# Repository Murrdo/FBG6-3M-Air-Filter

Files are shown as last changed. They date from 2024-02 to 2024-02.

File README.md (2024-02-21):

# FBG6-3M-Air-Filter
Air filter for FBG6

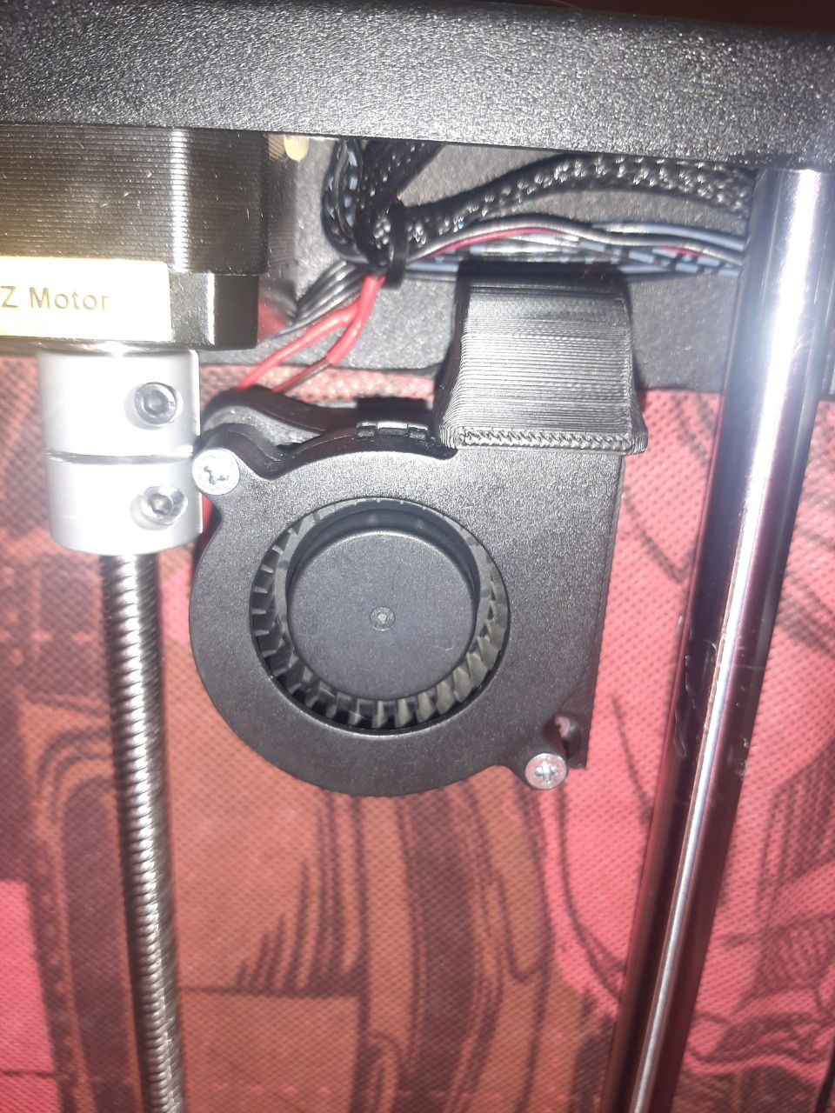
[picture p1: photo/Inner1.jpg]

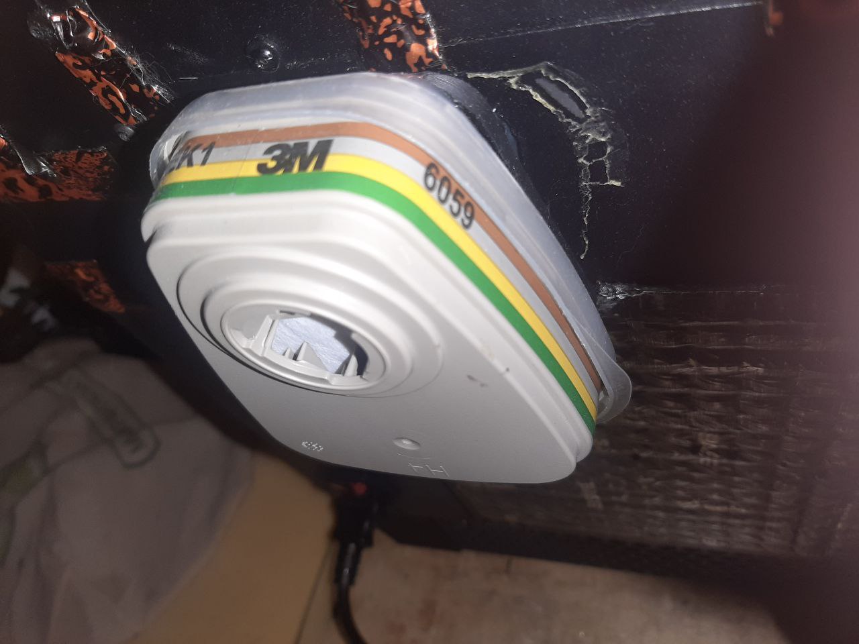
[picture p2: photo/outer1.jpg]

Фильтр для принтера FBG6 испоьзующий сменные фильтры 3M (проверено на 6059) - при условии общей герметизации запаха нет при 10 часовой печати в закрытой непроветриваемой комнате.

Подготовка и принцип действия.
<br>Фильтр работает при принципу "подпора" внешним давлением, т.е. во время работы вентилятор создаёт минимальное разряжение внутри, что бы через щели (которые в любом случае остануться) воздух снаружи поступал внутрь, а не выходил наружу. При этом ущерба темпиратуре в камере он не наносит.

Фильтр обазтельно требует акриловый колпак.

Что необходимо проклеить виброй или любым другим удобным материалом:
<br>1.Кромку примыкания двери и корпуса (очень мягкая вспененая резина толщиной 3мм)
<br>2.Колпак по периметру примыкания к корпусу (та же резина)
<br>3.Отсек с электроникой
<br>4.Щели на дне камеры
<br>5.Все отверстия под хомуты, под провод на датчик филамента и т.д. в общем вообще все мельчашие отверстия/щели/прорези, все что видите.

В норме запах наружу не попадает, т.е. например вплотную носом не ощущается запах у отверстия под трубку подачи филамента. Но при этом поток на выходу фильтра едва ощутим рукой.

Установка самого фильтра:

Внутренний блок под вентилятор 5015 обязательно перед установкой прокилеить по кромке примыкания к корпусу мягким двхсторонним скотчем, вентялтор можно посадить на клей типа б7000 (хотя это излишне). 
<br>Вентилятор вкручивается болтами на 2 вплавляемые втулки.
<br>Наружный блок так же по периметру примыкания к корпсу на скотч. 
<br>Крепление предфильтра 3м прикручивается на 6 болтов м3*5 в закладные, под него обазтельно нанести любой герметик по всей площади (B7000 прекрасно подойдёт) примыкания к креплению.

На данный момент первого фильтра хватило уже на 4 месяца довольно частой печати АБСом.

Пример организация управления фильтром, стартовый код Prusaslicer/Superslicer:
```
START_PRINT  EXTRUDER_TEMP={first_layer_temperature[0]} BED_TEMP={first_layer_bed_temperature[0]} MATERIAL={filament_type[0]}
```
Макрос и конфиг в klipper:

```
[fan_generic Filter_Fan]
pin: PD15
kick_start_time = 0.8
cycle_time = 0.025
```
Включение если идёт печать АБСом
```
[gcode_macro START_PRINT]
description = Start routine for the print
variable_retract = 6

gcode = 
	{% set extruder_temp = params.EXTRUDER_TEMP|default(240)|float %}
	{% set travel_temp = params.TRAVEL_TEMP|default(extruder_temp - 50 )|float %}
	{% set bed_temp = params.BED_TEMP|default(70)|float %}
	{% set MATERIAL = params.MATERIAL|default('PLA')|string %}
	CLEAR_PAUSE
	M220 S100 #сброс скорости печати на 100
	M221 S100
	G90 #установка абсолютных координат
	M82 #экструдер в абсолютный режим
	SET_HEATER_TEMPERATURE HEATER=extruder TARGET={travel_temp}
	SET_HEATER_TEMPERATURE HEATER=heater_bed TARGET={bed_temp}
	SET_FAN_SPEED FAN=Filter_Fan SPEED=0
	{% if MATERIAL == 'ABS' %}
		filter_on
   	{% endif %}
	G28
	TEMPERATURE_WAIT SENSOR=heater_bed MINIMUM={bed_temp}
	SET_HEATER_TEMPERATURE HEATER=extruder TARGET={extruder_temp}
	TEMPERATURE_WAIT SENSOR=extruder MINIMUM={extruder_temp}	
```

PS: Внешнюю часть можно сделать намного компактней, и на фото как раз доработанная версия, на спасибо фьюжену - эта версия не сохранилась, переделывать её модель снова лень уш простите.

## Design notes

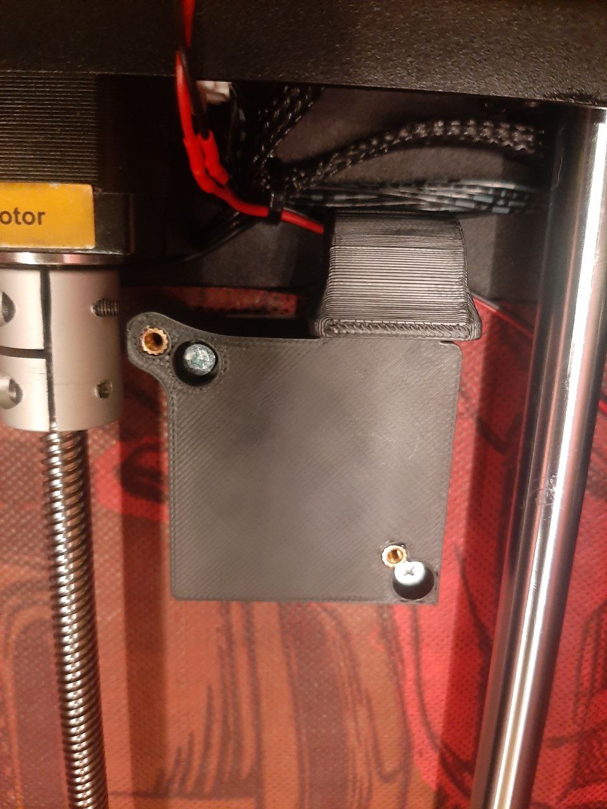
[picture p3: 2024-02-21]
photo/inner.jpg

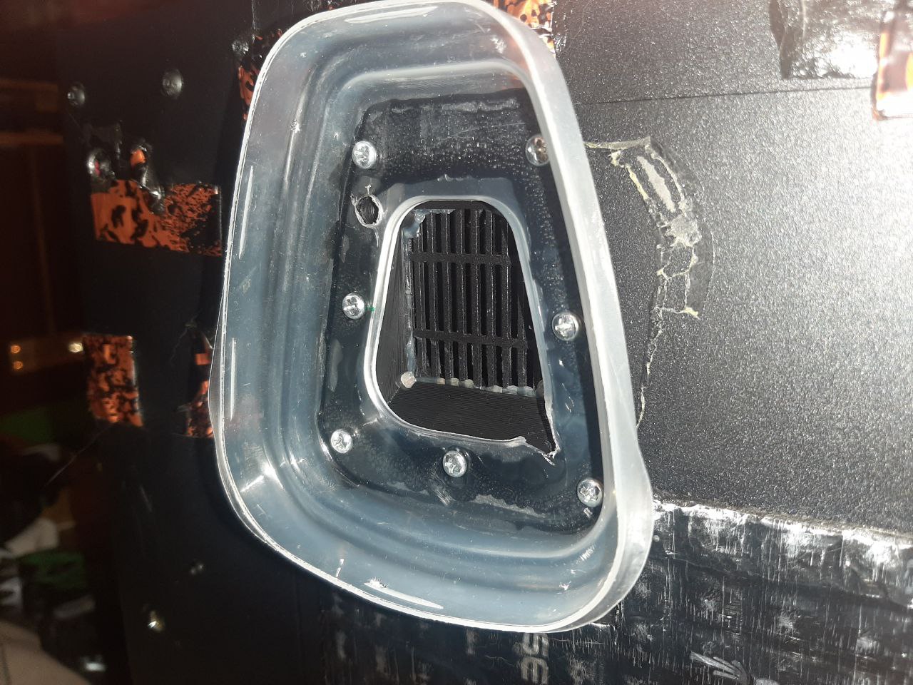
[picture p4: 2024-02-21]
photo/outer.jpg

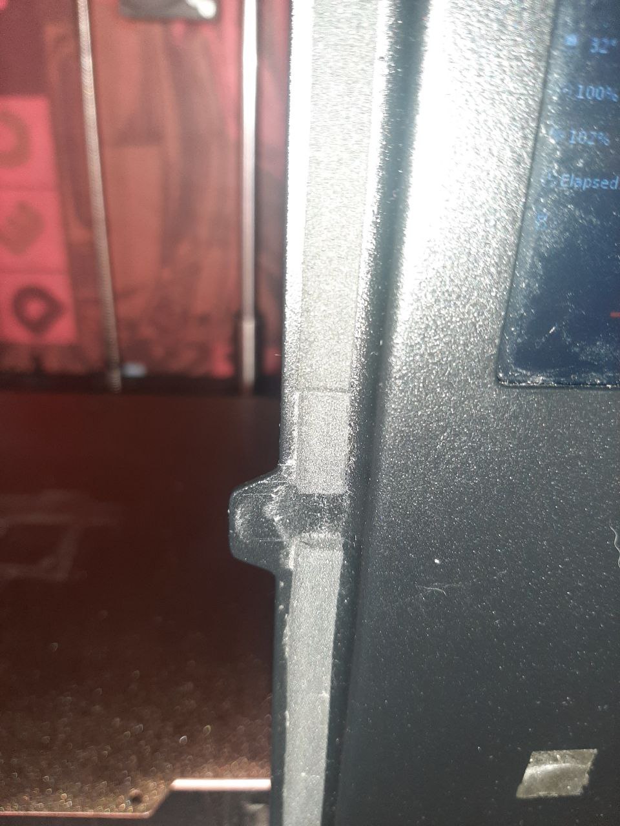
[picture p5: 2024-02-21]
photo/Пример уплотнения контура двери.jpg

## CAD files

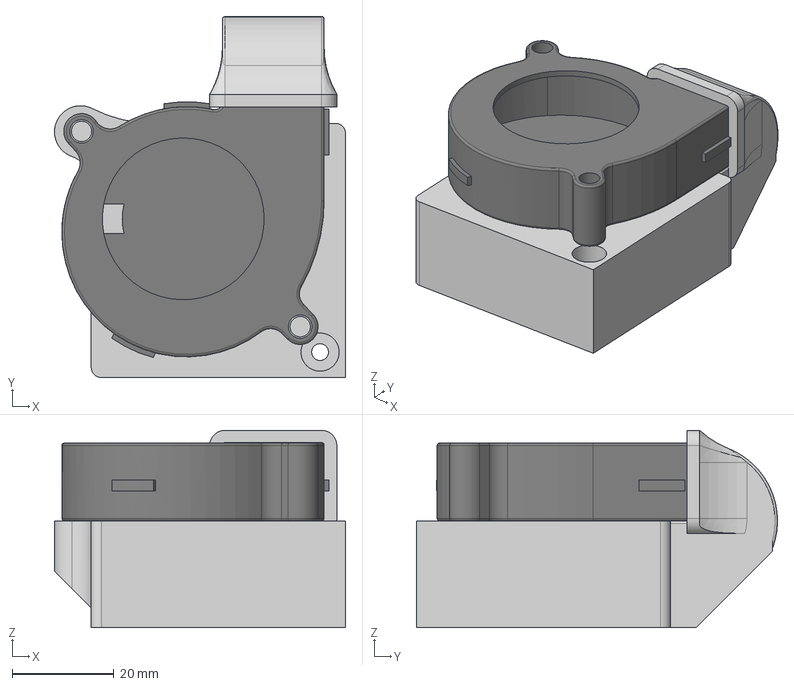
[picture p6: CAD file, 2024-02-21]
Air Filter FBG6 v3.step
57.2 x 71.0 x 38.8 mm

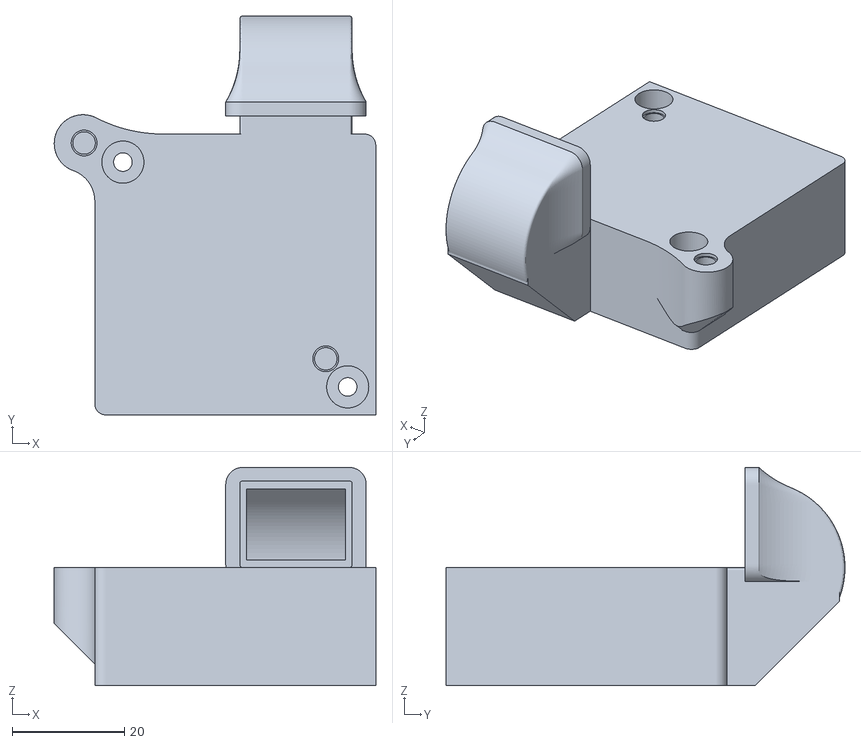
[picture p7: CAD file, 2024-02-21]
inner.stl
57.2 x 71.0 x 38.8

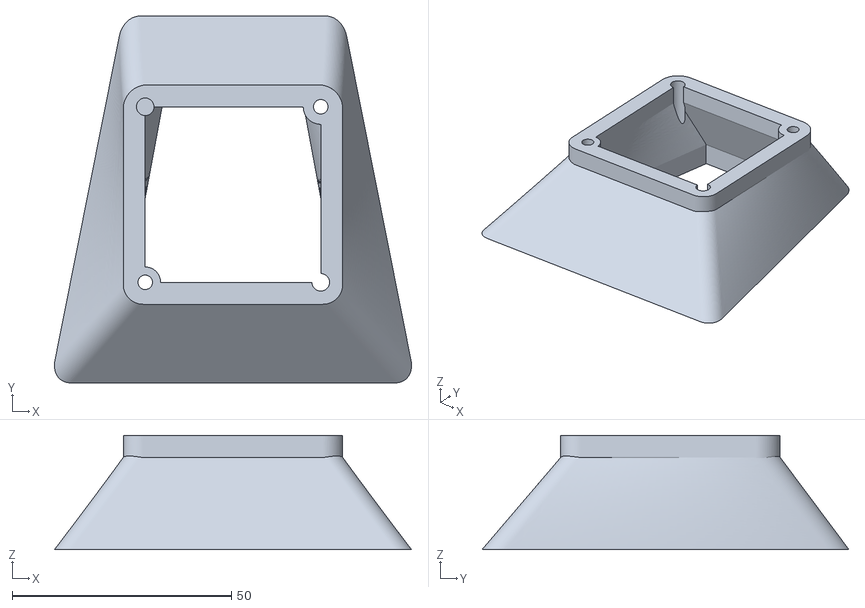
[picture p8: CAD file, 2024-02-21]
outer.stl
81.3 x 83.6 x 26.0

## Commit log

2024-02-21 Rename photo_2024-02-22_00-39-01.jpg to Пример уплотнения контура двери
2024-02-21 Rename Пример уплотнения контура двери to Пример уплотнения контура двери.jpg
2024-02-21 Rename Пример уплотнения контура двери.jpg to photo/Пример уплотнения контура двери.jpg
